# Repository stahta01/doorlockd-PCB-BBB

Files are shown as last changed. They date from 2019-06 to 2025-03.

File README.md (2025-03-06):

# doorlockd-PCB-BBB

Kicad drawing for doorlockd electronics on a Beagleboard black cape.
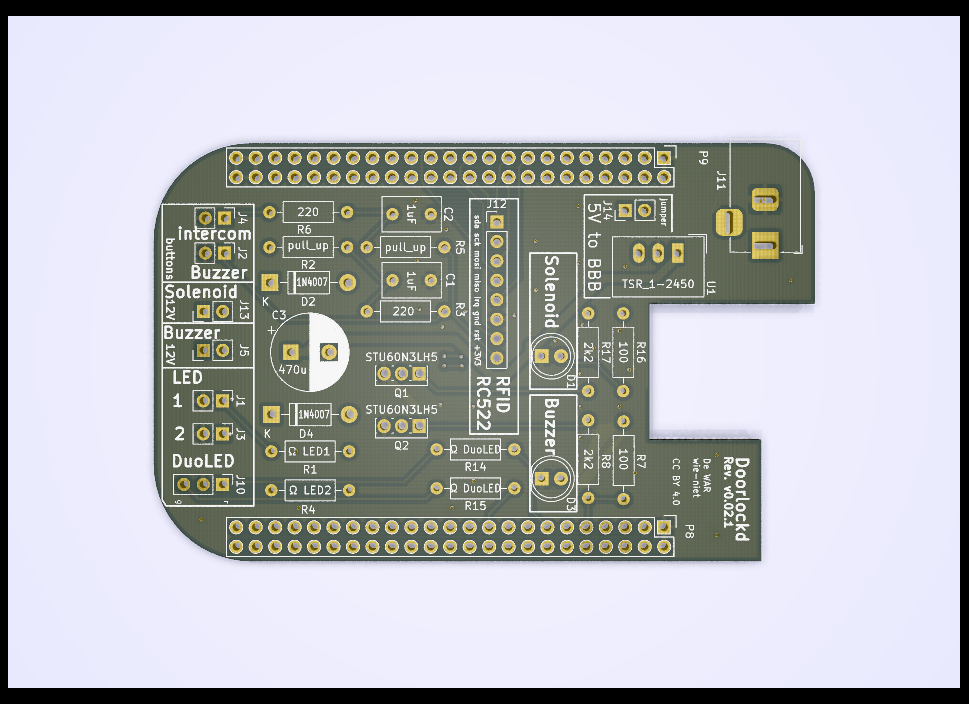
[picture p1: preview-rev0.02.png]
Preview doorlockd-PCB-BBB Rev0.02


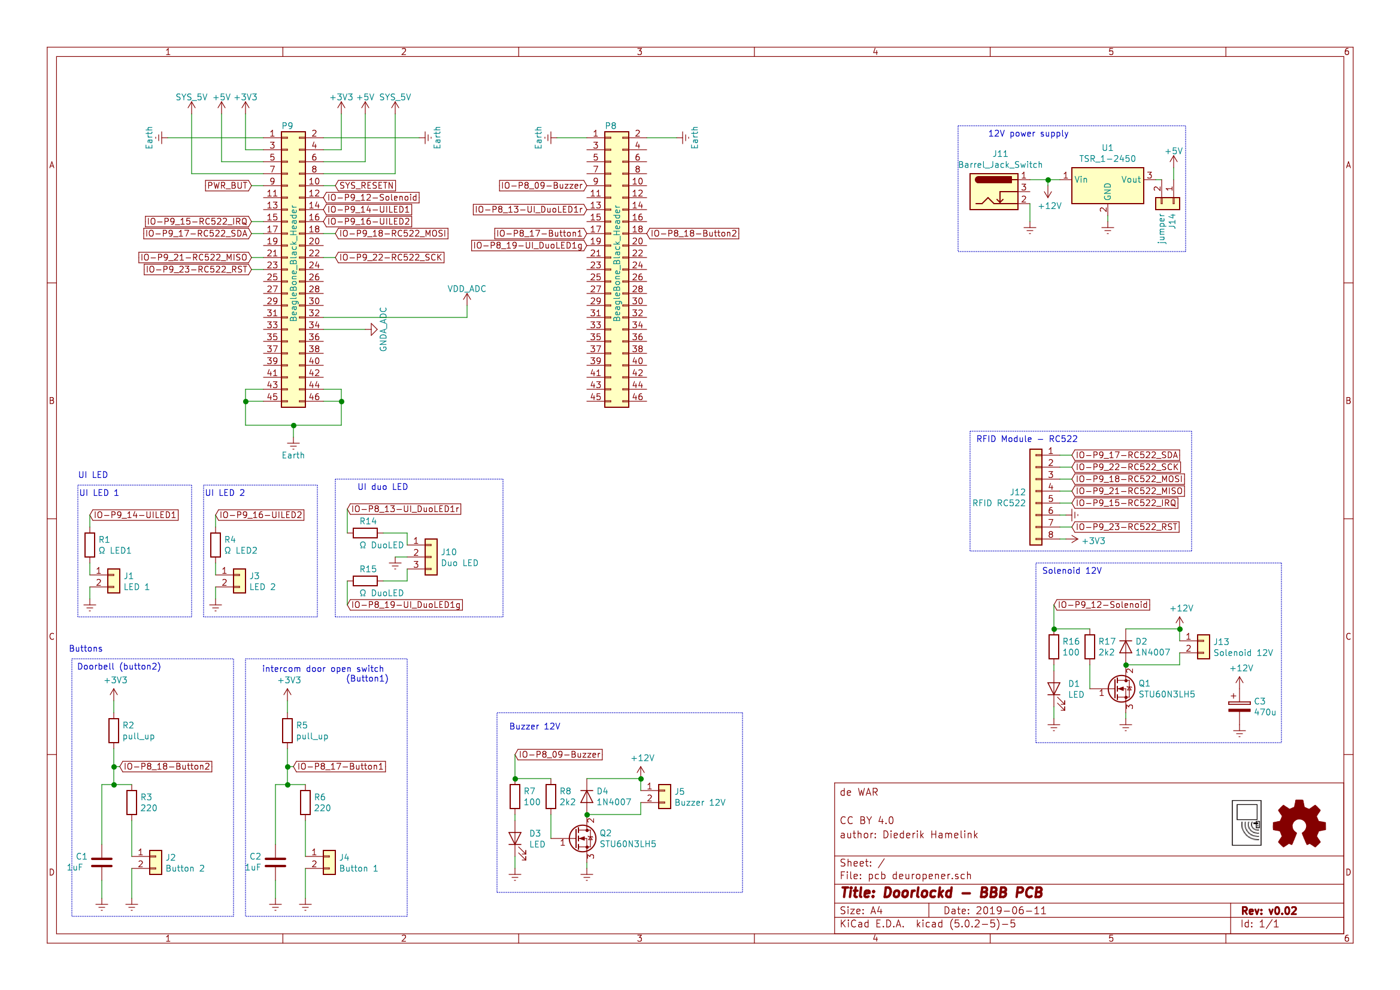
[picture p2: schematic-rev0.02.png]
Schema doorlockd-PCB-BBB Rev0.02
[](https://github.com/wie-niet/doorlockd-PCB-BBB/blob/master/schematic-rev0.02.pdf)

### component list
|Ref| |Value|
| --- | --- | --- |
|C1|C|1uF |
|C2|C|1uF|
|C3|CP|470u|
|D1|LED|LED|
|D2|1N4007|1N4007|
|D3|LED|LED|
|D4|1N4007|1N4007|
|J1|Conn_01x02|LED 1|
|J10|Conn_01x03|Duo LED|
|J11|Barrel_Jack_Switch|Barrel_Jack_Switch|
|J12|Conn_01x08|RFID RC522|
|J13|Conn_01x02|Solenoid 12V|
|J14|Conn_01x02|jumper|
|J2|Conn_01x02|Button 2|
|J3|Conn_01x02|LED 2|
|J4|Conn_01x02|Button 1|
|J5|Conn_01x02|Buzzer 12V|
|P8|Conn_02x23_Odd_Even|BeagleBone_Black_Header|
|P9|Conn_02x23_Odd_Even|BeagleBone_Black_Header|
|Q1|Q_NMOS_GDS|STU60N3LH5|
|Q2|Q_NMOS_GDS|STU60N3LH5|
|R1|R|Ω LED1 |
|R14|R|Ω DuoLED|
|R15|R|Ω DuoLED|
|R16|R|100|
|R17|R|2k2|
|R2|R|pull_up|
|R3|R|220|
|R4|R|Ω LED2|
|R5|R|pull_up|
|R6|R|220|
|R7|R|100|
|R8|R|2k2|
|U1|TSR_1-2450|TSR_1-2450|

#### LED resistor notes
Choose the resistors based on the LEDs you use.

|Led |resistors|
| --- | ---: |
|red | 100 ohm|
|green | 60 ohm|
|yellow | 48 ohm|
|blue |4 ohm|

### connected IO ports
| |port|chip,line<sup>\*1</sup>|name|
| --- | --- | --- | --- |
|IO|P8_17|gpiochip0 27|Button1|
|IO|P9_12|gpiochip1 28|Solenoid|
|IO|P9_14|gpiochip1 18|UILED1|
|IO|P8_18|gpiochip2 1|Button2|
|IO|P9_17|gpiochip0 5|RC522_SDA|
|IO|P9_22|gpiochip0 2|RC522_SCK|
|IO|P9_18|gpiochip0 4|RC522_MOSI|
|IO|P9_21|gpiochip0 3|RC522_MISO|
|IO|P9_15|gpiochip1 16|RC522_IRQ|
|IO|P9_23|gpiochip1 17|RC522_RST|
|IO|P8_13|gpiochip0 23|UI_DuoLED1r|
|IO|P8_19|gpiochip0 22|UI_DuoLED1g|
|IO|P9_16|gpiochip1 19|UILED2|
|IO|P8_9|gpiochip2 5|Buzzer|

<sub>*\*1):* GPIO Chip+line for gpiod, reference taken from https://elinux.org/Beagleboard:BeagleBone_cape_interface_spec </sub>

### Connecting PN532 board
This board was originally designed for use with the RC522 NFC reader,
but is also usable with the PN532 reader (which has better range and
reliability).

 - BBB SCK pin (`RC522_SCK`) is `UART2_RXD` -> connect to PN532 TX
 - BBB MISO pin (`RC522_MISO`) is `UART2_TXD` -> connect to PN532 RX
 - 5V can be taken from P9 pin 7 and/or 8 (needs extra pin soldered on)

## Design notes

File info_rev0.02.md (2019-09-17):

# Info on PCB deuropener rev0.02

# Notes/Bugs: 

## printed output names of "Buzzer" and "Solenoid" were mixed up. Fixed in rev0.02.1 [Issue #3](https://github.com/wie-niet/doorlockd-PCB-BBB/issues/3)
The printed names of Buzzer and Solenoid were mixed up in rev0.02. make sure you use J13 for Solenoid and J5 for Buzzer or doorbell.

# GPIO
```
IO	P8_17	Button1
IO	P8_18	Button2
IO	P8_09	Buzzer
IO	P9_15	RC522_IRQ
IO	P9_21	RC522_MISO
IO	P9_18	RC522_MOSI
IO	P9_23	RC522_RST
IO	P9_22	RC522_SCK
IO	P9_17	RC522_SDA
IO	P9_12	Solenoid
IO	P9_14	UILED1
IO	P9_16	UILED2
IO	P8_19	UI_DuoLED1g
IO	P8_13	UI_DuoLED1r
```

## Components 
```
C1		1uF 
C2		1uF
C3		470u
D1		LED (red)
D2		1N4007
D3		LED (red)
D4		1N4007
J1		PinHeader 01x02	LED 1
J2		PinHeader 01x02	Button 2
J3		PinHeader 01x02	LED 2
J4		PinHeader 01x02	Button 1
J5		PinHeader 01x02	Buzzer 12V
J10		PinHeader 01x03	Duo LED
J11		Barrel_Jack_Switch
J12		PinHeader 01x08	RFID RC522
J13		PinHeader 01x02	Solenoid 12V
J14		PinHeader 01x02	jumper + jumper
P8		BeagleBone_Black_Header 23x02	(backside)
P9		BeagleBone_Black_Header 23x02	(backside)
Q1		STU60N3LH5
Q2		STU60N3LH5
R1		Ω LED1 
R2		pull_up
R3		220
R4		Ω LED2
R5		pull_up
R6		220
R7		100
R8		2k2
R14		Ω DuoLED
R15		Ω DuoLED
R16		100
R17		2k2
U1		TSR_1-2450
```

### Ω LED 1,2,DuoLED
```
color	  ohm
red   	100 
green 	 60 
yellow	 48 
blue  	  4
```

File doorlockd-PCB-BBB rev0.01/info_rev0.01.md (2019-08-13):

# Info on PCB deuropener rev0.01

## Notes/Bugs: 

### Wrong pins used. Issue #2 
Disable the onboard harware in /boot/uEnv.txt:
	disable_uboot_overlay_video=1 
	disable_uboot_overlay_emmc=1
	disable_uboot_overlay_audio=1

### 12V barreljack connected to wrong pin. Issue #1
Quick fix is to create a bridge between pin3 and pin2 of the 12V barreljack.

## GPIO

   P8_01/02 GND
IO P8_21 Button2     ( MMC1_CLCK )
IO P8_23 Button1     ( MMC1_DAT4 )
IO P8_34 UILED1      ( LCD_DATA11 )
IO P8_36 UILED2      ( LCD_DATA10 )
IO P8_45 UI_BiLED1g  ( LCD_DATA0 )
IO P8_46 UI_BiLED1r  ( LCD_DATA1 )

   P9_01/02 GND
   P9_03/04 +3V3
   P9_05/06 +5V
IO P9_14 Solenoid
IO P9_15 RC522_IRQ
IO P9_17 RC522_SDA
IO P9_18 RC522_MOSI
IO P9_21 RC522_MISO
IO P9_22 RC522_SCK
IO P9_23 RC522_RST
IO P9_28 UI_TriLED1r ( MCASP0 .. (audio?) )
IO P9_42 UI_TriLED1g ( mcasp0_pins (audio?) )
   P9_43..46 GND

## Components 
C1    1uF Keramisch
C2	   1uF Keramisch
C3	   470u
D1	   LED
D2    1N4007
J1    Conn 01x02
J10	Conn 01x03
J11	Barrel Jack (Switch)
J12	Conn 01x08
J13	Conn 01x02
J14	Conn 01x02 + Jumper 
J2	   Conn 01x02
J3	   Conn 01x02
J4	   Conn 01x02
J8	   Conn 01x02
P8	   BeagleBone Black Header (Conn 23x02 backside of print) 
P9	   BeagleBone Black Header (Conn 23x02 backside of print) 
Q1	   STU60N3LH5
R1	   100 ohm   (ui led 1)
R11	R         (ui bicolor led) 
R14	R         (ui tricolor led red)
R15	R         (ui tricolor led green)
R16	100 ohm   (onboard led) 
R17	2k2 ohm         
R2	   pull up   (button 1)
R3	   220 ohm   (button 1)
R4	   100 ohm   (ui led 2)
R5	   pull up   (button 2)
R6	   220 ohm   (button 2)
U1	   TSR 1-2450

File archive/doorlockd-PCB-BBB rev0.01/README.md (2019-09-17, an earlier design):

# Info on PCB deuropener rev0.01

## Preview 
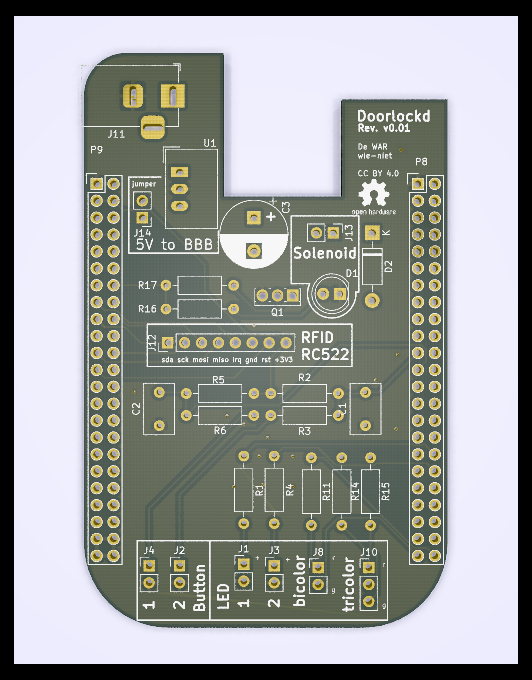
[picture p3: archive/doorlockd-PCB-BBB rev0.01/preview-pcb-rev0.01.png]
Preview doorlockd-PCB-BBB Rev0.01


PDF Preview of Schemantic [preview-schematic-rev0.01.pdf](https://github.com/wie-niet/doorlockd-PCB-BBB/blob/master/archive/doorlockd-PCB-BBB%20rev0.01/preview-schematic-rev0.01.pdf) on github.

## Notes/Bugs: 

### Wrong pins used. [Issue #2](https://github.com/wie-niet/doorlockd-PCB-BBB/issues/2)

Disable the onboard harware in `/boot/uEnv.txt`:
```
	disable_uboot_overlay_video=1 
	disable_uboot_overlay_emmc=1
	disable_uboot_overlay_audio=1
```
### 12V barreljack connected to wrong pin. [Issue #1](https://github.com/wie-niet/doorlockd-PCB-BBB/issues/1)
Quick fix is to create a bridge between pin3 and pin2 of the 12V barreljack.

## GPIO
```
   P8_01/02 GND
IO P8_21 Button2     ( MMC1_CLCK )
IO P8_23 Button1     ( MMC1_DAT4 )
IO P8_34 UILED1      ( LCD_DATA11 )
IO P8_36 UILED2      ( LCD_DATA10 )
IO P8_45 UI_BiLED1g  ( LCD_DATA0 )
IO P8_46 UI_BiLED1r  ( LCD_DATA1 )
   P9_01/02 GND
   P9_03/04 +3V3
   P9_05/06 +5V
IO P9_14 Solenoid
IO P9_15 RC522_IRQ
IO P9_17 RC522_SDA
IO P9_18 RC522_MOSI
IO P9_21 RC522_MISO
IO P9_22 RC522_SCK
IO P9_23 RC522_RST
IO P9_28 UI_TriLED1r ( MCASP0 .. (audio?) )
IO P9_42 UI_TriLED1g ( mcasp0_pins (audio?) )
   P9_43..46 GND
```

## Components 
```
C1    1uF Keramisch
C2	   1uF Keramisch
C3	   470u
D1	   LED
D2    1N4007
J1    Conn 01x02
J10	Conn 01x03
J11	Barrel Jack (Switch)
J12	Conn 01x08
J13	Conn 01x02
J14	Conn 01x02 + Jumper 
J2	   Conn 01x02
J3	   Conn 01x02
J4	   Conn 01x02
J8	   Conn 01x02
P8	   BeagleBone Black Header (Conn 23x02 backside of print) 
P9	   BeagleBone Black Header (Conn 23x02 backside of print) 
Q1	   STU60N3LH5
R1	   100 ohm   (ui led 1)
R11	R         (ui bicolor led) 
R14	R         (ui tricolor led red)
R15	R         (ui tricolor led green)
R16	100 ohm   (onboard led) 
R17	2k2 ohm         
R2	   pull up   (button 1)
R3	   220 ohm   (button 1)
R4	   100 ohm   (ui led 2)
R5	   pull up   (button 2)
R6	   220 ohm   (button 2)
U1	   TSR 1-2450
```

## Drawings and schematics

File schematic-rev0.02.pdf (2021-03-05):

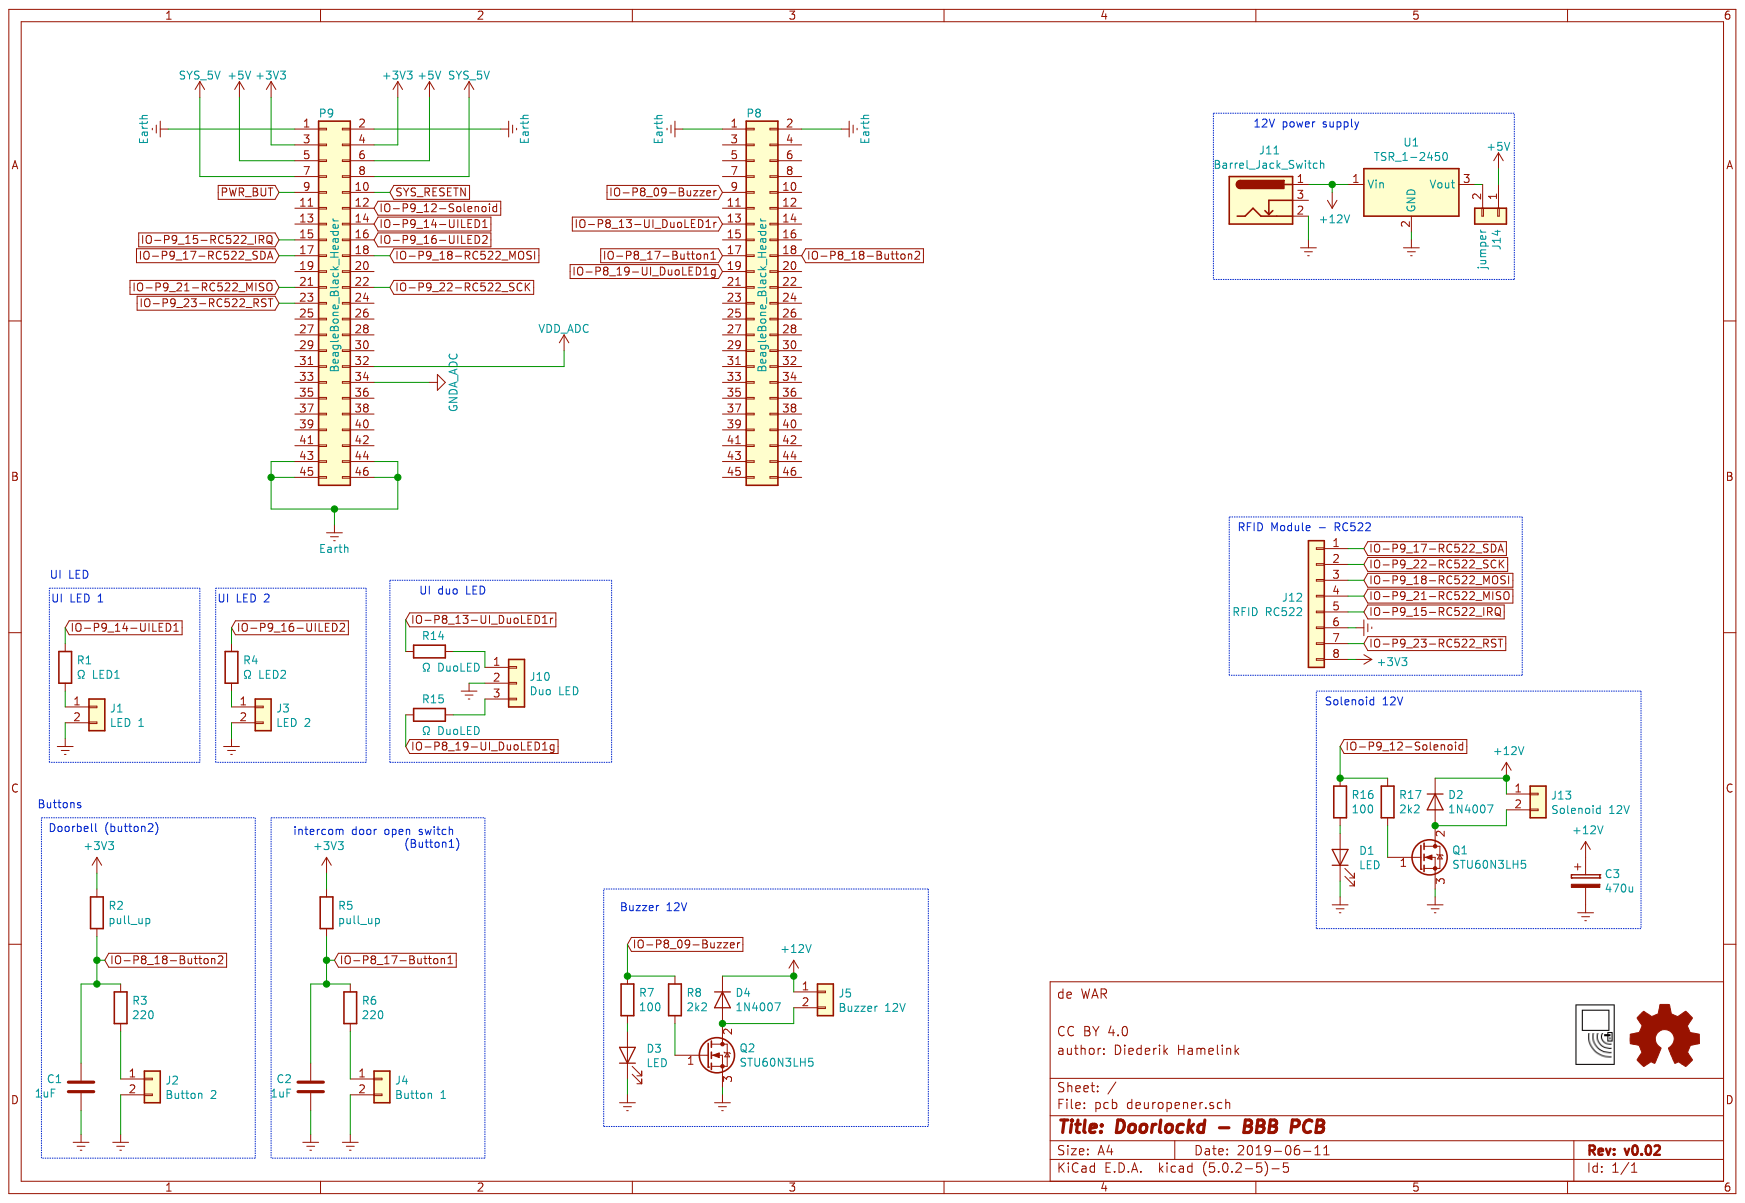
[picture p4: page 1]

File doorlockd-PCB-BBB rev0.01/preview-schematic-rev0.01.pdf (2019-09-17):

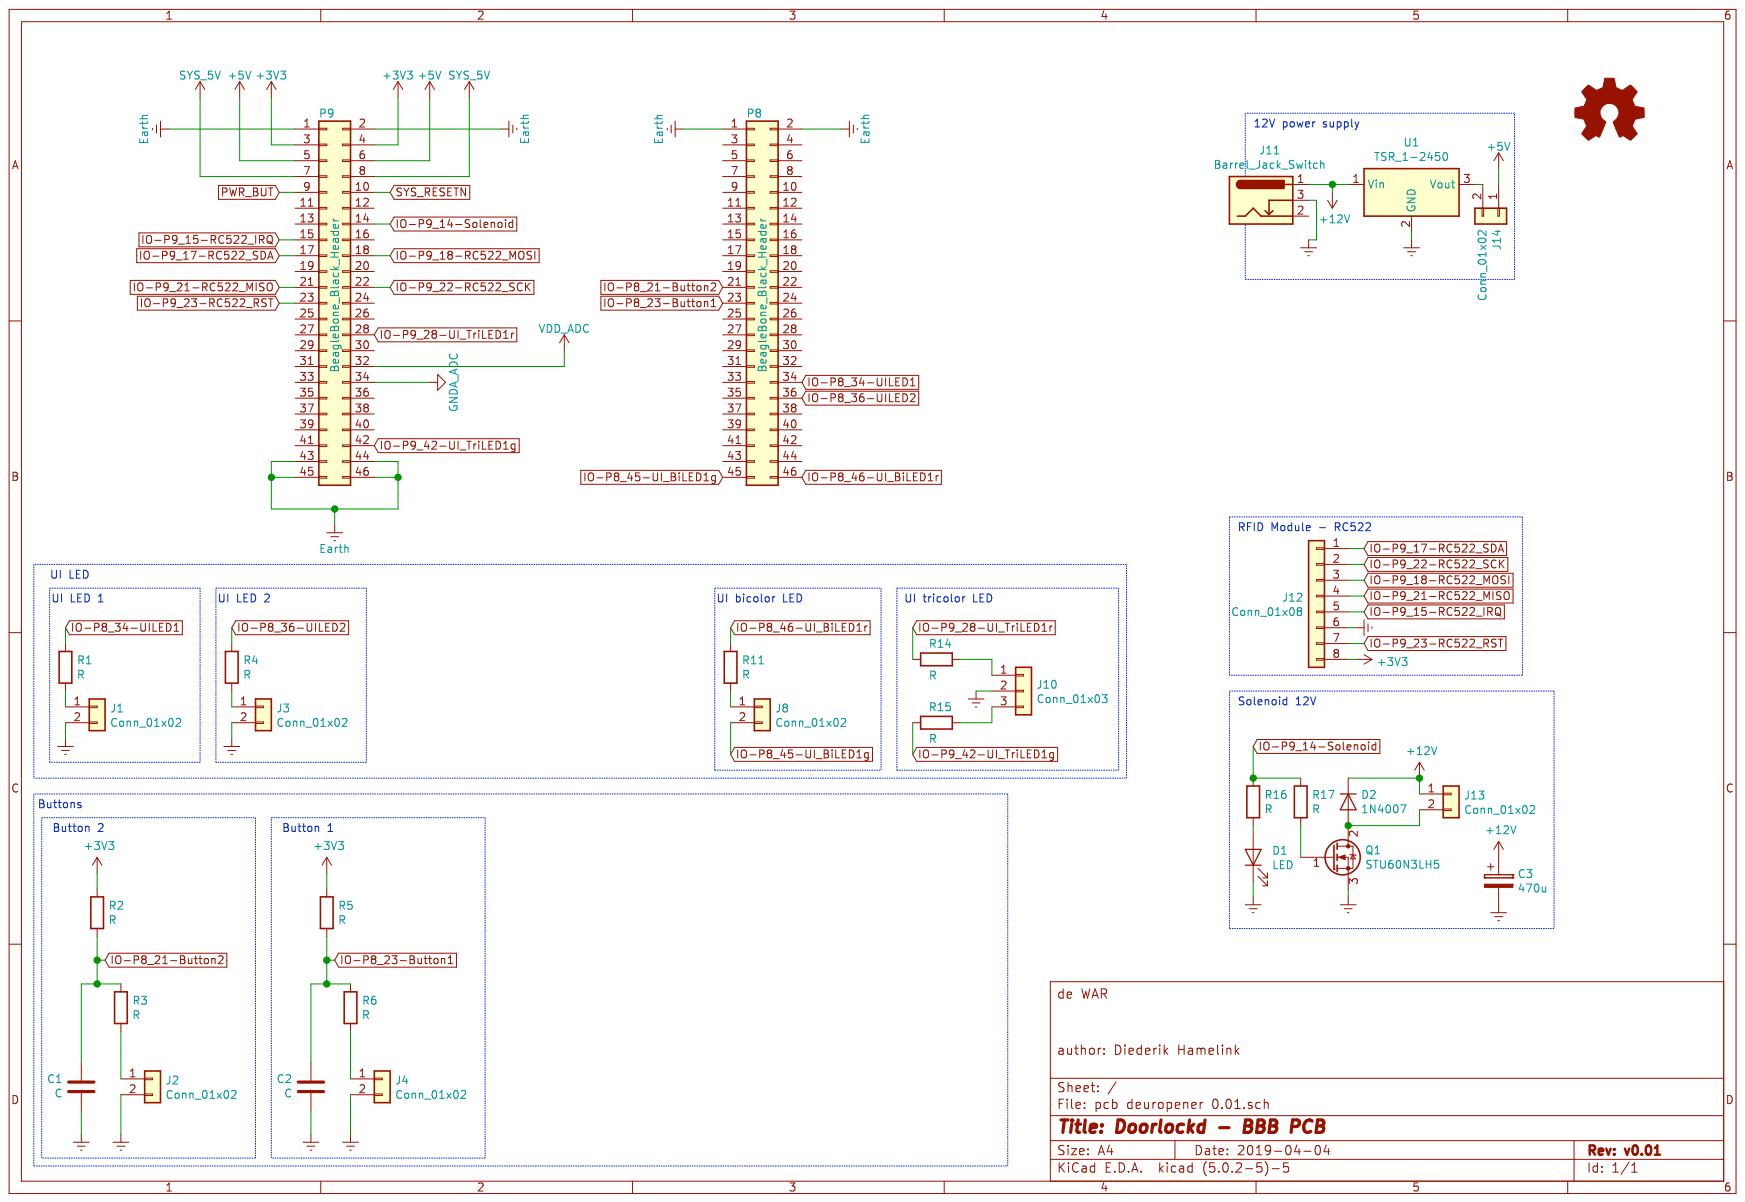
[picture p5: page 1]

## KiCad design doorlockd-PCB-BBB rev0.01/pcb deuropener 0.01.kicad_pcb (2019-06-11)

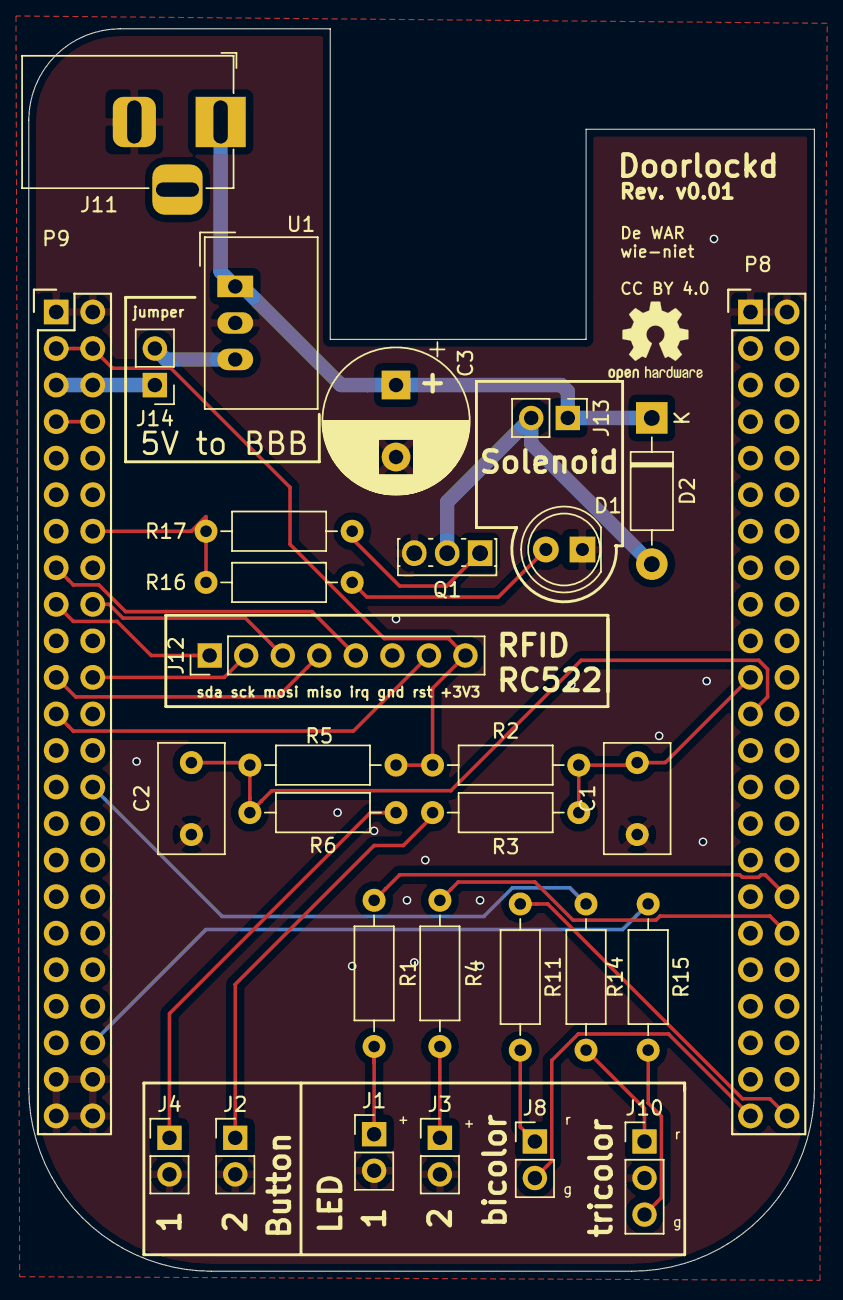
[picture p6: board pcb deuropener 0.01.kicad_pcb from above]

Board: 2 copper layers, 54.6 x 86.4 mm, 30 parts (0 on the bottom side), 31 nets.

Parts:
C1, C2: C; C_Disc_D7.5mm_W4.4mm_P5.00mm
C3: 470u; CP_Radial_D10.0mm_P5.00mm
D1: LED; LED_D5.0mm
D2: 1N4007; D_DO-41_SOD81_P10.16mm_Horizontal
J1, J2, J3, J4, J8, J13, J14: Conn_01x02; PinHeader_1x02_P2.54mm_Vertical
J10: Conn_01x03; PinHeader_1x03_P2.54mm_Vertical
J11: Barrel_Jack_Switch; BarrelJack_Horizontal
J12: Conn_01x08; PinHeader_1x08_P2.54mm_Vertical
P8, P9: BeagleBone_Black_Header; Socket_BeagleBone_Black
Q1: STU60N3LH5; SIPAK_Vertical
R1, R2, R3, R4, R5, R6, R11, R14, R15, R16, R17: R; R_Axial_DIN0207_L6.3mm_D2.5mm_P10.16mm_Horizontal
U1: TSR_1-2450; Converter_DCDC_TRACO_TSR-1_THT

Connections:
+3V3: J12.8, P9.3, P9.4, R2.1, R5.1
+5V: J14.1, P9.5, P9.6
+12V: C3.1, D2.1, J11.1, J13.1, U1.1
Earth: C1.1, C2.1, C3.2, D1.1, J1.2, J2.2, J3.2, J4.2, J10.2, J11.2, J12.6, P8.1, P8.2, P9.1, P9.2, P9.43, P9.44, P9.45, P9.46, Q1.3, U1.2
IO-P8_21-Button2: C1.2, P8.21, R2.2, R3.1
IO-P8_23-Button1: C2.2, P8.23, R5.2, R6.1
IO-P8_34-UILED1: P8.34, R1.1
IO-P8_36-UILED2: P8.36, R4.1
IO-P8_45-UI_BiLED1g: J8.2, P8.45
IO-P8_46-UI_BiLED1r: P8.46, R11.1
IO-P9_14-Solenoid: P9.14, R16.1, R17.1
IO-P9_15-RC522_IRQ: J12.5, P9.15
IO-P9_17-RC522_SDA: J12.1, P9.17
IO-P9_18-RC522_MOSI: J12.3, P9.18
IO-P9_21-RC522_MISO: J12.4, P9.21
IO-P9_22-RC522_SCK: J12.2, P9.22
IO-P9_23-RC522_RST: J12.7, P9.23
IO-P9_28-UI_TriLED1r: P9.28, R14.2
IO-P9_42-UI_TriLED1g: P9.42, R15.2
unnamed: D1.2, R16.2
unnamed: D2.2, J13.2, Q1.2
unnamed: J1.1, R1.2
unnamed: J2.1, R3.2
unnamed: J3.1, R4.2
unnamed: J4.1, R6.2
unnamed: J8.1, R11.2
unnamed: J10.1, R14.1
unnamed: J10.3, R15.1
unnamed: J14.2, U1.3
unnamed: Q1.1, R17.2
SYS_5V: P9.7, P9.8

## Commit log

2019-05-21 First prototype rev v0.01
    [pcb deuropener 0.01.kicad_pcb, pcb deuropener 0.01.sch]
2019-06-11 Fixed: 12V barreljack connected to wrong pin #1
    [pcb deuropener 0.01.sch]
2019-06-11 OSHW Logo was removec after last change, re-added (Place >> Footprint >> "search OSHW" and place the smalles logo on print).
    [pcb deuropener 0.01.kicad_pcb]
2019-07-16 A lot of changes to rev 0.02
    [pcb deuropener 0.01.kicad_pcb, pcb deuropener.kicad_pcb, pcb deuropener.sch]
2019-07-16 A lot of changes for rev0.02 and fix for issue #2
    [pcb deuropener.kicad_pcb, pcb deuropener.sch]
2019-07-30 Better Earth track to FETs and Capacitor
    [pcb deuropener.kicad_pcb]
2019-07-30 improved Earth path and 12V path to the southern area of the pcb.
    [pcb deuropener.kicad_pcb]
2019-08-13 Documentation file added with GPIO port information and component list with values. in info_rev0.01.txt
    [pcb deuropener.kicad_pcb, pcb deuropener.sch]
2019-08-13 resistor values per LED color
2019-09-10 fixed mix up of printed names "Solenoid" and "Buzzer". nothing changed to electronics #3
    [pcb deuropener.kicad_pcb]
2019-09-17 Archive of rev0.01 including preview images of pcb and schematics
    [pcb deuropener 0.01.kicad_pcb, pcb deuropener 0.01.sch]
2019-09-17 moved doorlockd-PCB-BBB rev0.01 into archive folder
    [pcb deuropener 0.01.kicad_pcb, pcb deuropener 0.01.sch]
2021-03-05 add schematic
2021-03-05 add schematic preview

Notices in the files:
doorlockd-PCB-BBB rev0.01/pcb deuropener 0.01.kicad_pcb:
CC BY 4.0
